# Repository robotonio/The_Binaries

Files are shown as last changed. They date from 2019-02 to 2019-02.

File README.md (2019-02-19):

# The_Binaries
This is the research project of "The Binaries" team, in the FLL "INTO ORBIT" competition, in 2019. The project's object is the exploitation of "Soft Robotics" technology in space and for this purpose, the team has developed a system which compares the pros and cons of soft &amp; hard grippers.

The name of the S/H system comes from the words Soft vs. Hard (actuators).
The main purpose of the system is to show some of the advantages of Soft Robotics in the field of actuators. The above objective should not be construed as an attempt to prove that soft actuators are "better" than traditional actuators (hard), as Soft Robotics can not substitute current technology but can help address specific problems. The system is controlled by a central console, as well as remote control (Bluetooth) via an Android application developed for that purpose.

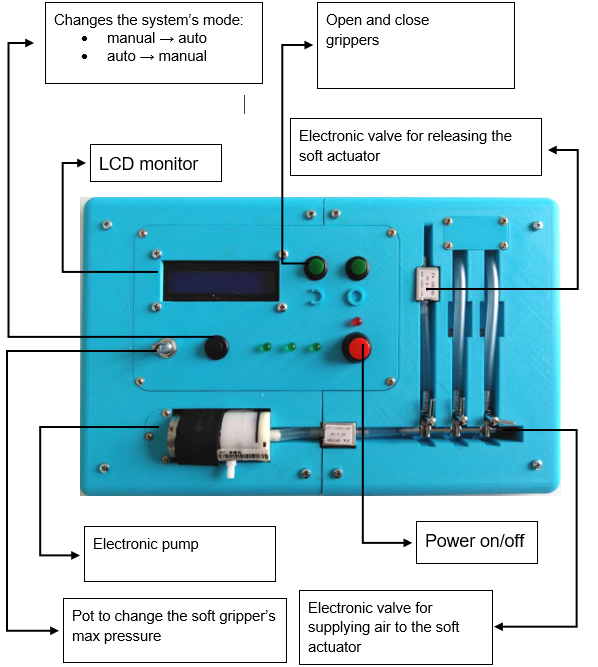
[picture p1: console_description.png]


The system is activated with the red button (B.1). When in operation, the red LED (L.1) is on, otherwise off. When the system is turned on, the THE BINARIES message appears on the LCD for 3 seconds, then the default function, which is "MANUAL," appears on the first line of the screen. The operation of the system can be changed to "AUTO" by pressing the black button (B.2) and returns to "MANUAL" in the same way.

• "MANUAL" mode: the actuators (soft & hard) open and close by pressing the green buttons B.3 & B.4 respectively. When the system is in "MANUAL" mode, the first green LED (L.2) is lit.

• "AUTO" mode: each actuator automatically closes when the ultrasonic sensor detects an object. The actuator remains closed until button B.3 is pressed. When the system is in "AUTO" mode, the second green LED (L.3) is lit.

There are also three manual air switches in the console. The first switch (S.1) should always be open to allow the Soft Actuator to bleed out. The second and third allow the air supply to the Soft Actuator to which they are connected. If the 1st actuator is used, the first switch (S.2) must be open and the 2nd switch (S.3) closed. The S.2 & S.3 switches must be inverted to activate the 2nd soft actuator.

There is also the third green LED (L.4) on the console that lights when a Bluetooth device is connected to the system. Finally, under the LCD, there is a potentiometer (P.1) used to adjust the air pressure that closes the soft actuator. The procedure for setting the pressure is as follows: the user presses B.3 for 5 seconds until "CHANGE PRESSURE" appears in the display. Then the potentiometer adjusts the desired pressure and by pressing the same button (B.3) saves the new selection.

During the operation of the system, the following useful messages are displayed on the LCD:
• During the process of setting the maximum actuator pressure, the current ("Current: #") and the new pressure ("New: #") are displayed on the LCD, where # numbers between 0 and 100.
• "HARD CLOSE" is displayed during the Hard Actuator closing process.
• The "HARD OPEN" message appears during the Hard Actuator opening process.
• In the closing procedure of the Soft Actuator, "SOFT CLOSE" appears on the first line of the LCD and the current Soft Actuator is pressed in the second.
• "SOFT OPEN" appears during the Soft Actuator opening process.

# Android APP

The Android application "THE BINARIES" has been developed for the needs of the system, which displays various measurements performed by the system and remote control of the opening and / or closing of the actuators.
The main features of the application are described below:

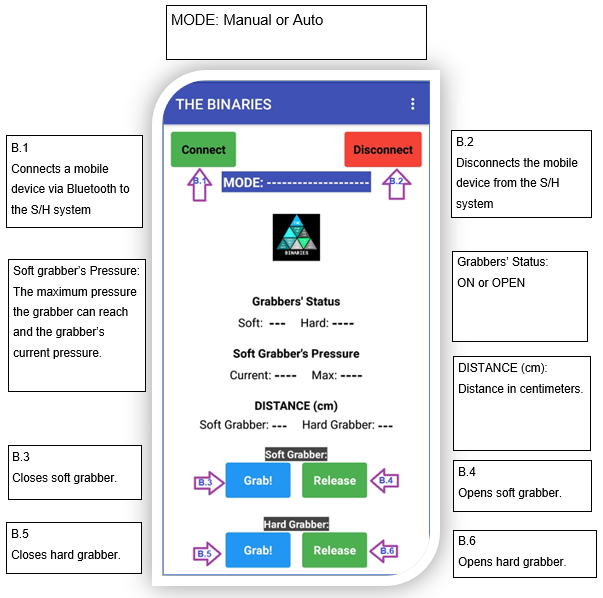
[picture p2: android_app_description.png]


# Microcontroller

The system controlled by the ESP32 microprocessor, witch has built in Bluetooth and WiFi capabilities, that make this electronic board not only autonomous to support automation but also compared to other platforms (such as those in the Arduino range), much more efficient and complete.

# Circuit

The following figure shows the system connection:

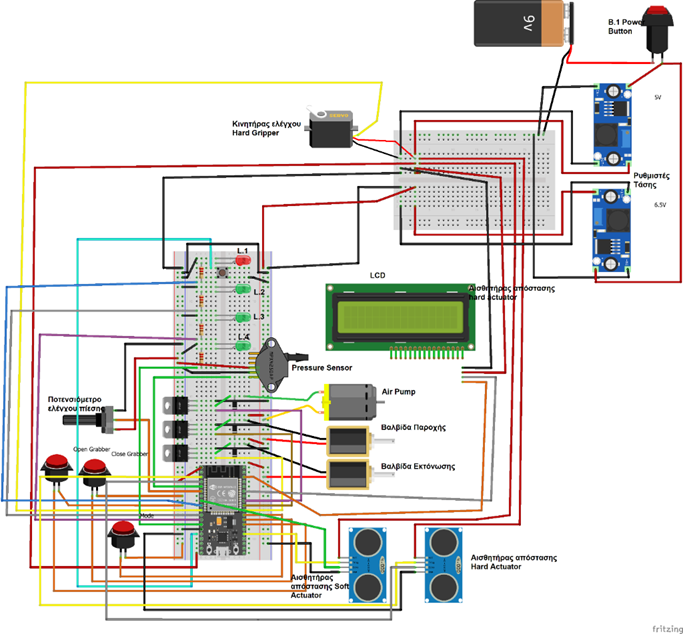
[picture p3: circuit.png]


# Sources

For the design and development of the system were used opensource sources that helped at each stage. Some of them:
1. The inspiration for the project was largely the Soft Robotics Toolkit, developed in a research conducted at Harvard University and Dublin Trinity College, which focused on the development of training kits for practical design lessons. The basic actuator control unit was based on the project "Low cost Electro-pneumatic circuit for Soft Robots", where we implemented the air supply and exhaust system in the Soft Actuator.
2. The soft actuators were built according to the instructions of the project "Air-Powered Soft Robotic Gripper" from the Instructables website.
3. For the development of the Android application-to-application code for the application (system and application side), it helped the project "ESP32 BLE + Android + Arduino IDE = AWESOME" from the Instructables website.
4. In developing the core part of the ESP32 program, he helped a lot with Adel Kassah's TUNIOT FOR ESP32 visual programming tool, based on Google's Blockly

• Soft Robotics Toolkit: https://softroboticstoolkit.com/home

• "Low cost Electro-pneumatic circuit for Soft Robots": https://softroboticstoolkit.com/low-cost-ep-circuit

• "Air-Powered Soft Robotic Gripper": https://www.instructables.com/id/Air-Powered-Soft-Robotic-Gripper/

• "ESP32 BLE + Android + Arduino IDE = AWESOME": https://www.instructables.com/id/ESP32-BLE-Android-App-Arduino-IDE-AWESOME/

• TUNIOT FOR ESP32: http://easycoding.tn/esp32/demos/code/

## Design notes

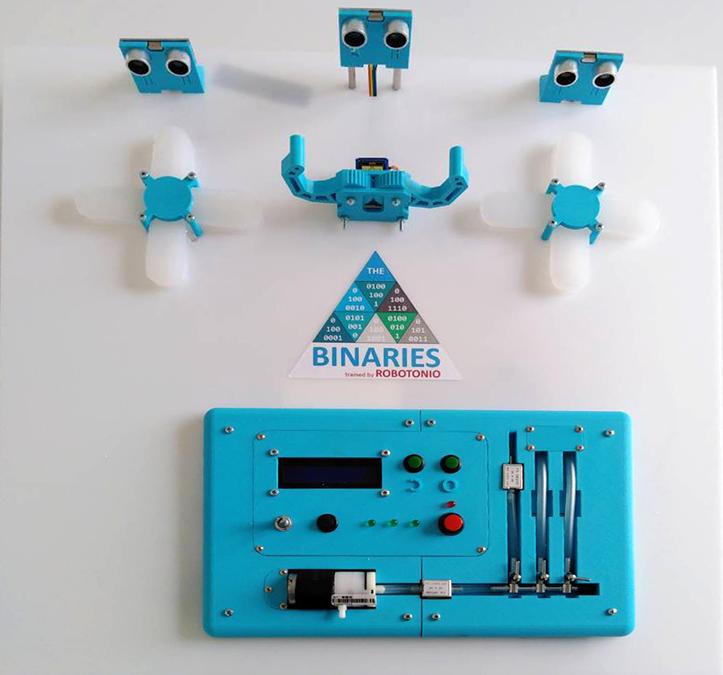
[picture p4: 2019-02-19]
console_image.jpg

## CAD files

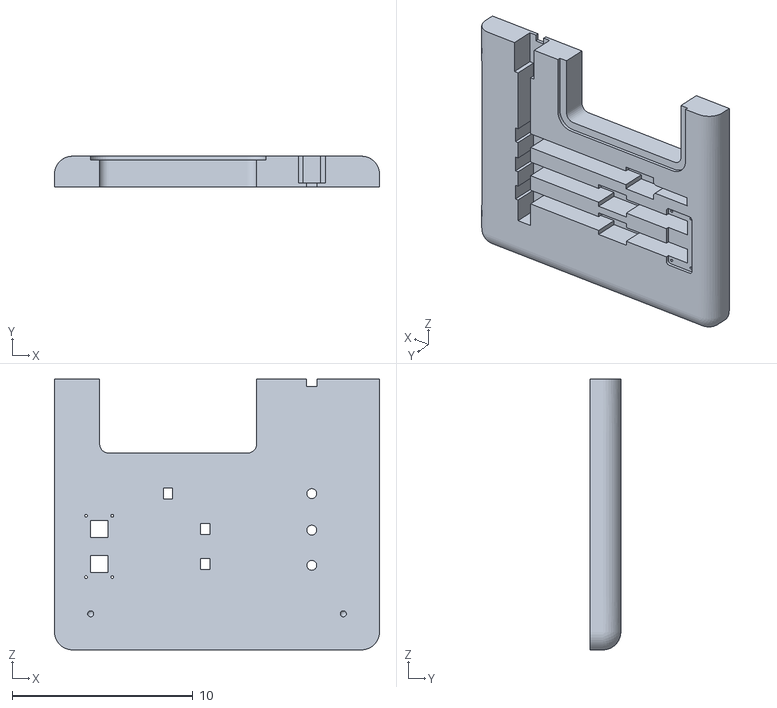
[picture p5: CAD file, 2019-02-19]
stl_files/Assembly1.stl
18.0 x 1.70 x 15.0

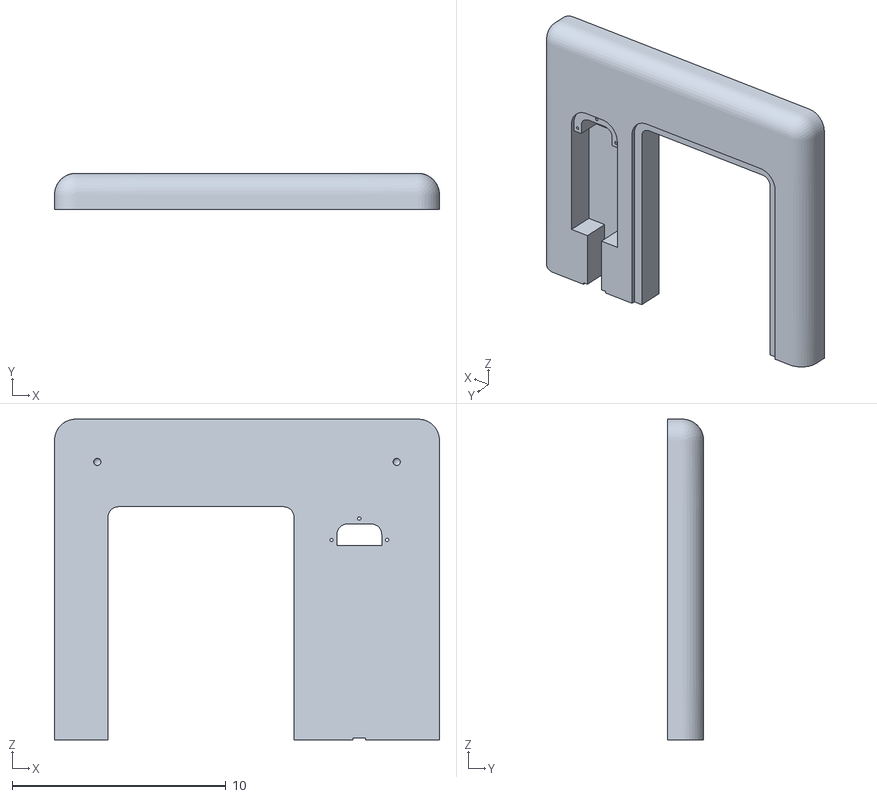
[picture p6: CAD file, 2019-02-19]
stl_files/Assembly2.stl
18.0 x 1.70 x 15.0

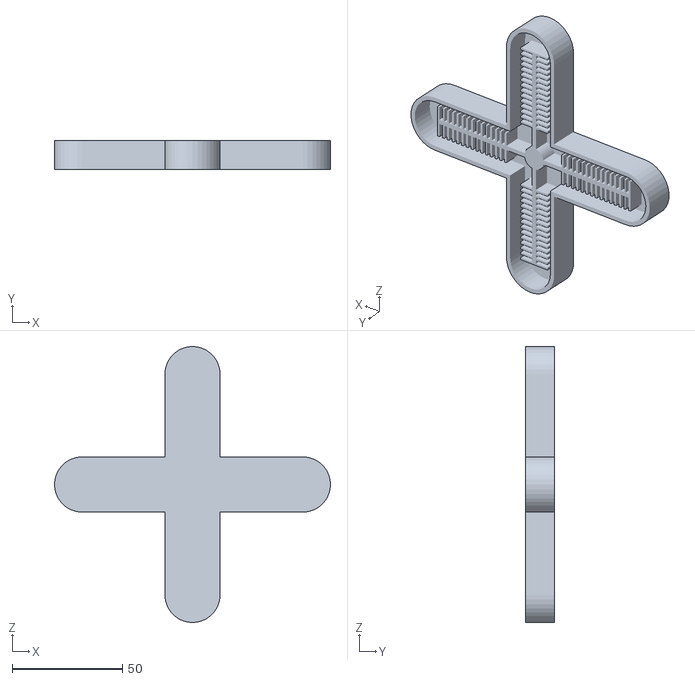
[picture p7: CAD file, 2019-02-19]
stl_files/4-leg-gripper.stl
125.0 x 13.0 x 125.0

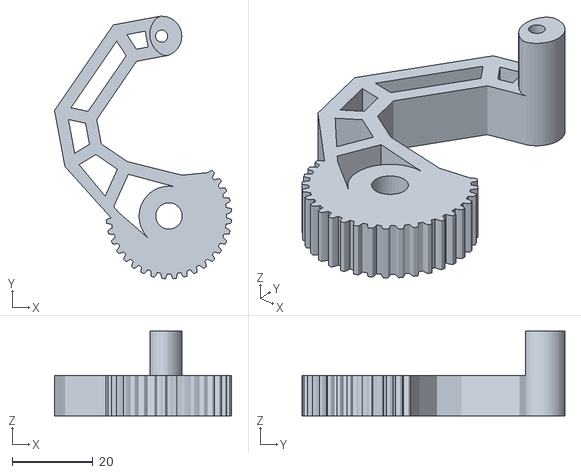
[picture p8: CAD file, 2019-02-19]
stl_files/stl_hard_gripper/finger-left-thin.stl
44.0 x 65.2 x 21.0

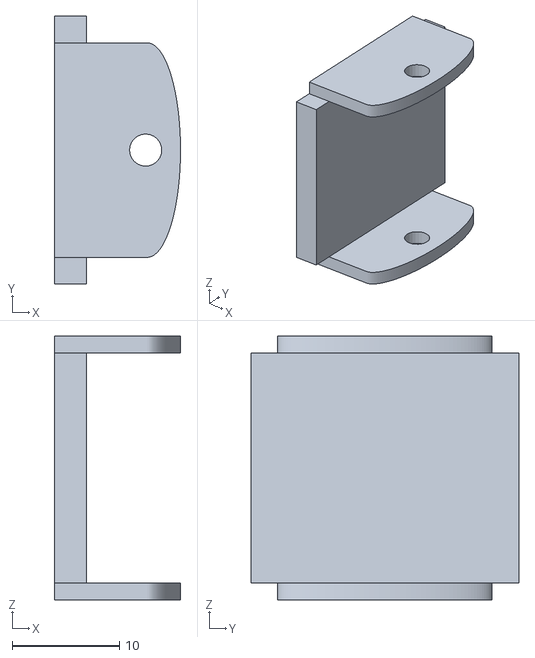
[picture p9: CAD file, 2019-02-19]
stl_files/stl_hard_gripper/finger-pad.stl
11.8 x 25.0 x 24.6

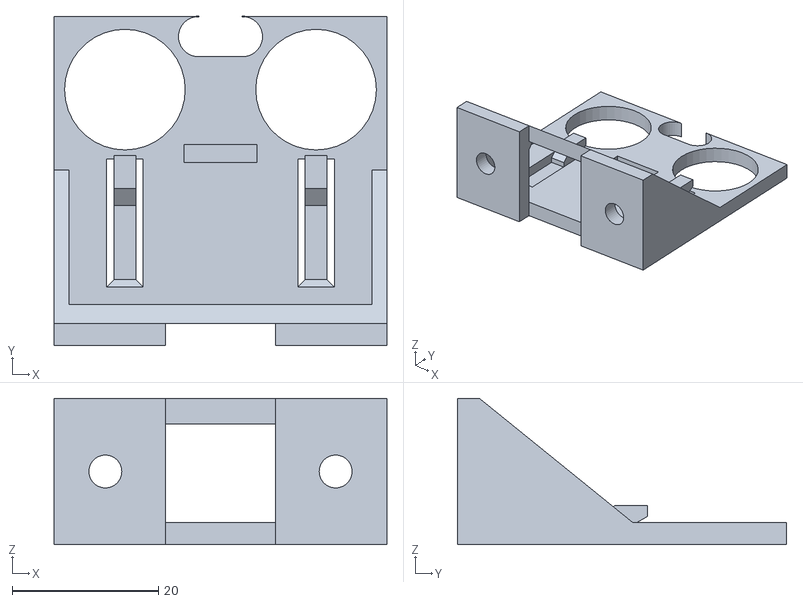
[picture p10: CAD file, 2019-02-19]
stl_files/Ultrasonic_HC-SR04_-_FOOT_MOUNT.stl
45.5 x 45.0 x 20.0

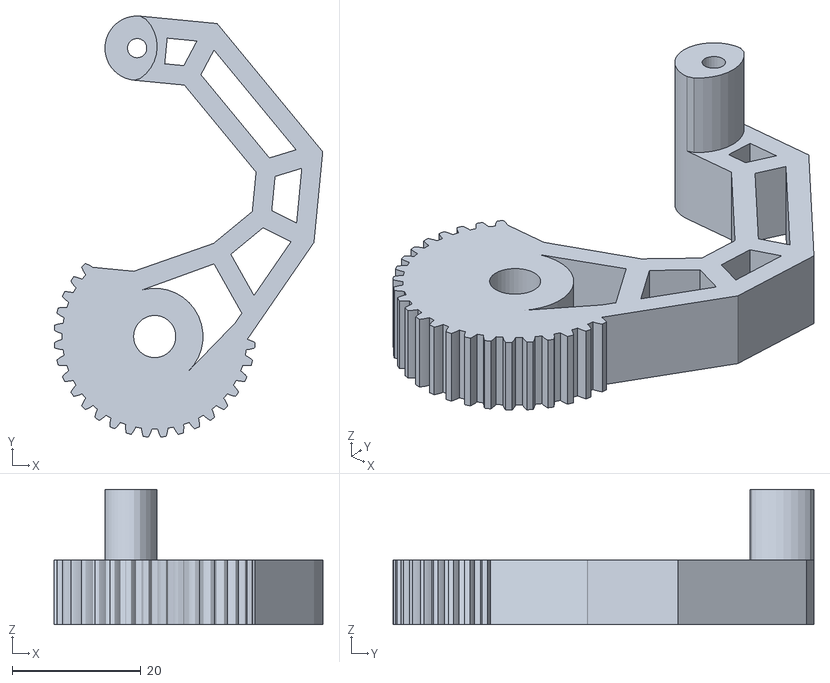
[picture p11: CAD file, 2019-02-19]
stl_files/stl_hard_gripper/finger-right-thin.stl
41.7 x 65.4 x 21.0

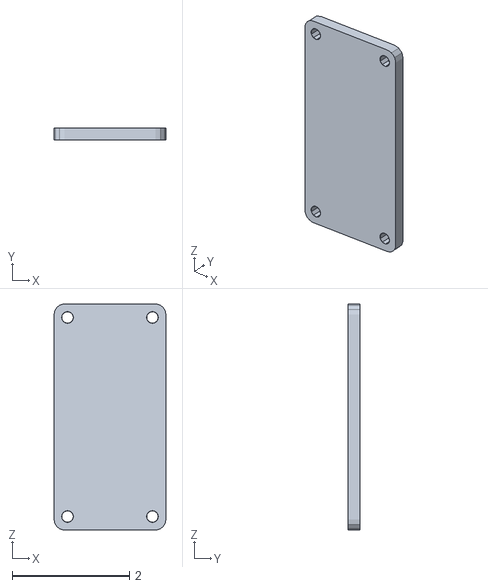
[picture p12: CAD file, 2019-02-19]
stl_files/Part2 base.stl
1.91 x 0.2 x 3.86

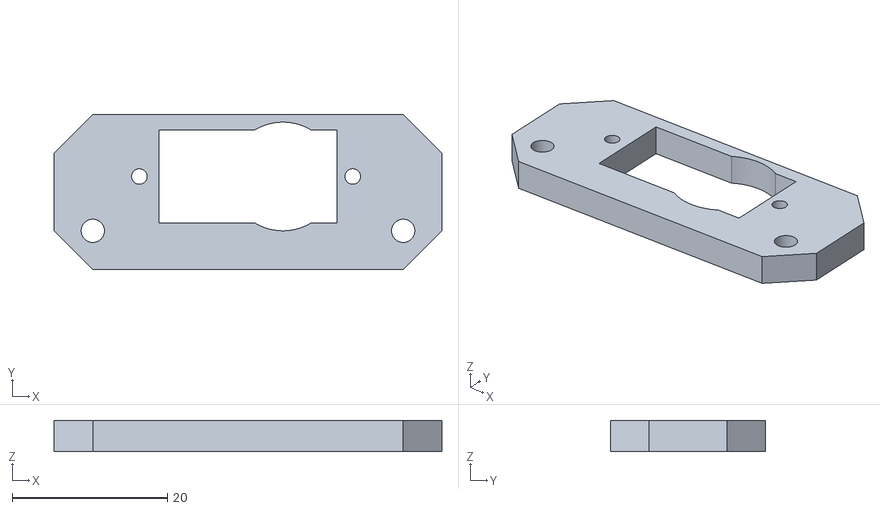
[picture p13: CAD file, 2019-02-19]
stl_files/stl_hard_gripper/servo-spacer-bigger.stl
50.0 x 20.0 x 4.00

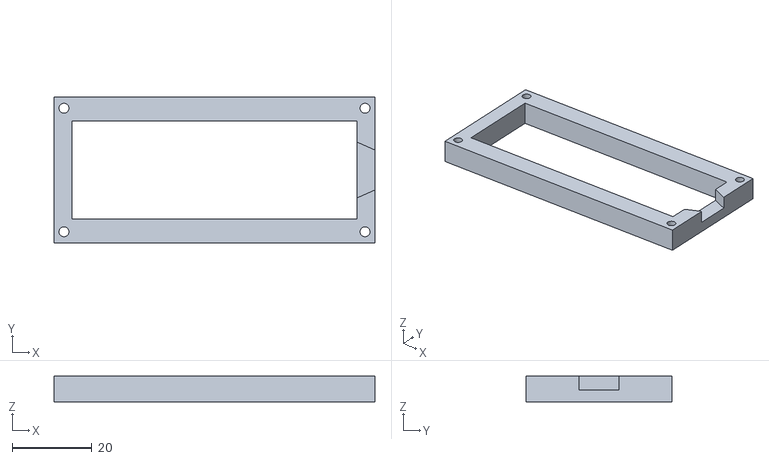
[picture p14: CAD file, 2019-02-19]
stl_files/lcd spacer.stl
80.5 x 36.5 x 6.50

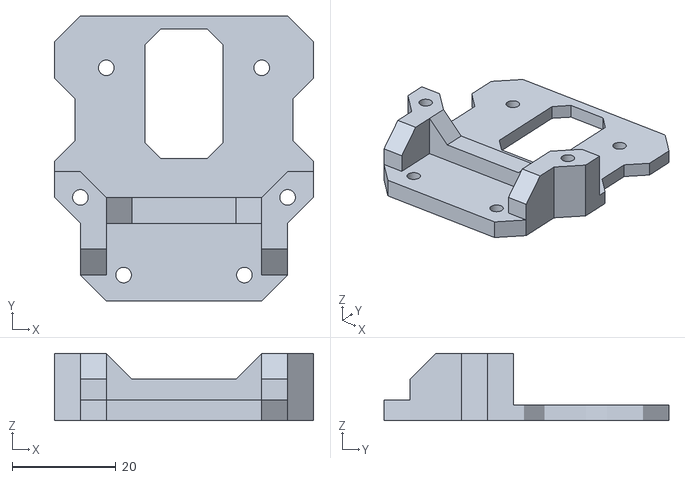
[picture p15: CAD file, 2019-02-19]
stl_files/stl_hard_gripper/gripper-base-thin.stl
50.0 x 55.0 x 13.0

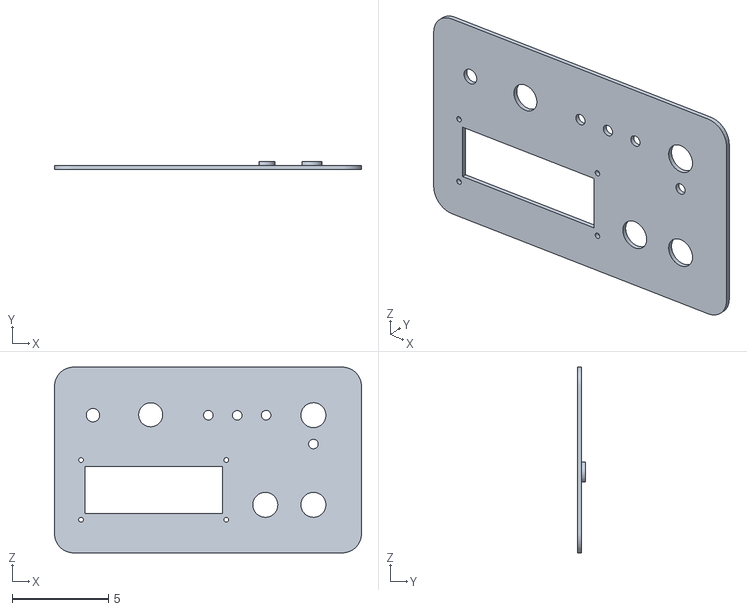
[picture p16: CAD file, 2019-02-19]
stl_files/lcd.stl
16.0 x 0.4 x 9.66

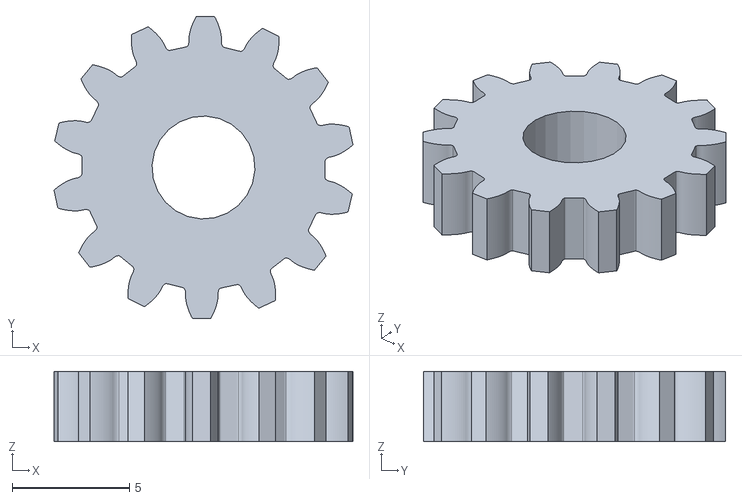
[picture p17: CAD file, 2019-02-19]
stl_files/stl_hard_gripper/servo-gear.stl
12.8 x 12.9 x 3.00

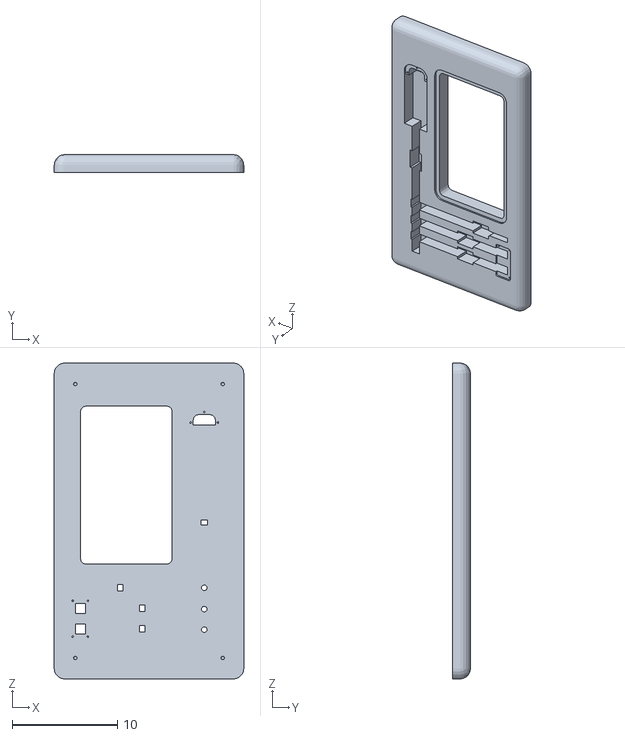
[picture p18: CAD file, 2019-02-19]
stl_files/Project FLL 2019 Base Final.stl
18.0 x 1.70 x 30.0

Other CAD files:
stl_files/stl_hard_gripper/top-plate-fixed.stl
stl_files/Part1 base.stl
stl_files/stl_hard_gripper/finger-bushing-thin.stl
stl_files/stl_hard_gripper/test.stl
stl_files/stand soft cross.stl

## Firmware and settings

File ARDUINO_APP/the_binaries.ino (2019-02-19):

#include <BLEDevice.h>
#include <BLEServer.h>
#include <BLEUtils.h>
#include <BLE2902.h>
#include <Servo.h>
#include <LiquidCrystal_I2C.h> //for LCD I2C

/* Bluetooth configuration*/
BLECharacteristic *pCharacteristic;
bool deviceConnected = false;
// See the following for generating UUIDs:
// https://www.uuidgenerator.net/
#define SERVICE_UUID           "6E400001-B5A3-F393-E0A9-E50E24DCCA9E" // UART service UUID
#define CHARACTERISTIC_UUID_RX "6E400002-B5A3-F393-E0A9-E50E24DCCA9E"
#define CHARACTERISTIC_UUID_TX "6E400003-B5A3-F393-E0A9-E50E24DCCA9E"

/*
 * usefull variables
*/
// max soft grabber's pressure in  
int maxPressure = 25; //calibrate it! (< 100)
int modeNumber = 1; //mode = 1 in setup
int previousMode = 1; //keep previous mode to know new change
//the max and min servo angle for hard actuator (calibrate it!)
int servoOpenDegrees = 180;//close
int servoCloseDegrees = 50;//open
//the distance threshold than actuate soft grabber in cm (calibrate it!)
int actDistanceSoft = 10;
//the distance threshold than actuate hard grabber in cm (calibrate it!)
int actDistanceHard = 10;
//flag for soft actuator (open/closed)
boolean softIsOpen = true;
//flag for hard actuator (open/closed)
boolean hardIsOpen = true;
long lastBTms = 0;//last communication with bluetooth 
long btSlot = 1000; //send bluetooth data every btSlot milliseconds
char BT_data[23];//buffer to keep data for bluetooth devices
long interruptTime = 0;
boolean interruptFlag = true;

void releaseSoft();
void releaseHard();
void grabSoft();
void grabHard();
bool is_number(const std::string& s);
class MyServerCallbacks: public BLEServerCallbacks {
    void onConnect(BLEServer* pServer) {
      deviceConnected = true;
    };

    void onDisconnect(BLEServer* pServer) {
      deviceConnected = false;
    }
};

class MyCallbacks: public BLECharacteristicCallbacks {
    void onWrite(BLECharacteristic *pCharacteristic) {
      std::string rxValue = pCharacteristic->getValue();

      if (rxValue.length() > 0) {
        Serial.println("*********");
        Serial.print("Received Value: ");

        for (int i = 0; i < rxValue.length(); i++) {
          Serial.print(rxValue[i]);
        }

        Serial.println();

        // Do stuff based on the command received from the app
        if (rxValue.find("S0") != -1) { 
          Serial.print("Soft Release");
          releaseSoft();
        } else if (rxValue.find("S1") != -1) { 
          Serial.print("Soft Grab");
          grabSoft();
        } else if (rxValue.find("H0") != -1) { 
          Serial.print("Hard Release");
          releaseHard();
        } else if (rxValue.find("H1") != -1) { 
          Serial.print("Hard Grab");
          grabHard();
        } else {
          Serial.print("New pressure");
          int newMaxPressure = atoi(rxValue.c_str());//std::stoi(rxValue);
          if(newMaxPressure > 0 && newMaxPressure < 100){
            maxPressure = newMaxPressure;
          }
        }

        Serial.println();
        Serial.println("*********");
      }
    }
};


LiquidCrystal_I2C lcd(0x3f, 16, 2);
Servo servo;

/*
 * Modes:
 *  1: on / off buttons (same for soft & hard gribbers)
 *  2: ultrasonic sensor use
 *  3: bluetooth use
*/

/*
 * All the pins
*/
// power button
int pinLedPower = 25;
// on-off buttons mode LED
int pinLedMode1 = 12;
// ultrasonic mode LED
int pinLedMode2 = 14;
// bluetooth mode LED
int pinLedMode3 = 4;
// change mode button
int pinModeBtn = 17;
// pressure configuration pot
int pinPressurePot = 35;
// change max pressure button
int pinPressureButton = 13;
// open grippers button
int pinOpenButton = 27;
// close grippers button
int pinCloseButton = 16;
// pressure sensor
int pinPressureSensor = 34;
// servo motor
int pinServo = 26;
// solenoid inflate gripper
int pinSolenoidInflate = 5;
// solenoid expansion gripper
int pinSolenoidExpanse = 18;
// dc motor (to close soft gripper)
int pinMotor = 19;
// Ultrasonic for soft gripper
int pinTrigHcSoft = 36;//2;
int pinEchoHcSoft = 39;//33;
// Ultrasonic for hard gripper
int pinTrigHcHard = 2;//36;
int pinEchoHcHard = 33;//39;
// Ultrasonic for 2nd soft gripper
int pinTrigHcSoft2 = 32;
int pinEchoHcSoft2 = 15;



/*
 * This function is triggered when a new
 * interrupt happens. In this way we change
 * the mode, using the mode button
*/
void handleModeInterrupt(){
  //move modeNumber to next mode
  interruptTime = millis();
  if(interruptFlag){
    modeNumber++;
    //max modeNumber is 2
    if(modeNumber > 2){
      modeNumber = 1;
    }
  }
}

void setup() {
  Serial.begin(115200);
  //configure servo for hard actuator
  servo.attach(pinServo);
  servo.write(servoOpenDegrees);//in setup hard actuator is closed
  //configure LCD
  lcd.init();
  lcd.backlight();
  //configure soft Ultrasonic Sensor
  pinMode(pinTrigHcSoft, OUTPUT); // Sets the trigPin as an Output
  pinMode(pinEchoHcSoft, INPUT); // Sets the echoPin as an Input
  //configure soft Ultrasonic Sensor
  pinMode(pinTrigHcSoft2, OUTPUT); // Sets the trigPin as an Output
  pinMode(pinEchoHcSoft2, INPUT); // Sets the echoPin as an Input
  //configure hard Ultrasonic Sensor
  pinMode(pinTrigHcHard, OUTPUT); // Sets the trigPin as an Output
  pinMode(pinEchoHcHard, INPUT); // Sets the echoPin as an Input
  //configure LEDs
  pinMode(pinLedPower, OUTPUT);
  pinMode(pinLedMode1, OUTPUT);
  pinMode(pinLedMode2, OUTPUT);
  pinMode(pinLedMode3, OUTPUT);
  //configure buttons
  pinMode(pinModeBtn, INPUT_PULLUP);
  pinMode(pinOpenButton, INPUT_PULLUP);
  pinMode(pinCloseButton, INPUT_PULLUP);
  pinMode(pinPressureButton, INPUT_PULLUP);
  //configure motors
  pinMode(pinSolenoidInflate, OUTPUT);
  pinMode(pinSolenoidExpanse, OUTPUT);
  pinMode(pinMotor, OUTPUT);

  //initialise actuators (all closed)
  digitalWrite(pinSolenoidInflate, LOW);
  digitalWrite(pinSolenoidExpanse, LOW);
  digitalWrite(pinMotor, LOW);

  //initialise LEDs (in setup mode=1)
  digitalWrite(pinLedPower, HIGH);//never changes
  digitalWrite(pinLedMode1, HIGH);
  digitalWrite(pinLedMode2, LOW);
  digitalWrite(pinLedMode3, LOW);
  setMode(modeNumber);
  //configure interrupt to change mode
  attachInterrupt(digitalPinToInterrupt(pinModeBtn), handleModeInterrupt, FALLING);

  /* Bluetooth set up*/
  // Create the BLE Device
  BLEDevice::init("THE_BINARIES"); // Give it a name

  // Create the BLE Server
  BLEServer *pServer = BLEDevice::createServer();
  pServer->setCallbacks(new MyServerCallbacks());

  // Create the BLE Service
  BLEService *pService = pServer->createService(SERVICE_UUID);

  // Create a BLE Characteristic
  pCharacteristic = pService->createCharacteristic(
                      CHARACTERISTIC_UUID_TX,
                      BLECharacteristic::PROPERTY_NOTIFY
                    );
                      
  pCharacteristic->addDescriptor(new BLE2902());

  BLECharacteristic *pCharacteristic = pService->createCharacteristic(
                                         CHARACTERISTIC_UUID_RX,
                                         BLECharacteristic::PROPERTY_WRITE
                                       );

  pCharacteristic->setCallbacks(new MyCallbacks());

  // Start the service
  pService->start();

  // Start advertising
  pServer->getAdvertising()->start();

  /* End bluetooth configuration*/
}

void loop() {
  //check id modeNumber changed to update the system mode
  if(millis() - interruptTime > 1000){
    interruptFlag = true;
  }
  if(previousMode != modeNumber){
    digitalWrite(pinSolenoidExpanse, HIGH);
    interruptFlag = false;
    setMode(modeNumber);
    previousMode = modeNumber;//update previousMode
  }
  //mode options
  if(modeNumber == 1){//move actuators with buttons
    runMode1();
  } else if(modeNumber == 2){//grab with sensor and free with button
    runMode2();
  }
  //check pressure button to change max pressure
  if(digitalRead(pinPressureButton) == LOW){
    Serial.println("pinPressureButton pressed");
    controlMaxPressure();    
  }

  if(millis() - lastBTms > btSlot){
    bluetoothApp();
    lastBTms = millis();
  }
}

/*
 * Control both actuators with the 
 * grab&free buttons
*/
void runMode1(){
  if(digitalRead(pinOpenButton) == LOW){
    long openTime = millis();
    boolean pressureMode = false;
    while(digitalRead(pinOpenButton) == LOW){
      if(millis() - openTime > 3000){
        pressureMode = true;
        break;
      } 
    }
    if(pressureMode){
      controlMaxPressure();
    } else {
      Serial.println("open button");
      releaseSoft();
      releaseHard();
      delay(500); 
    }
  }
  if(digitalRead(pinCloseButton) == LOW){
    Serial.println("close button");
    grabSoft();
    grabHard();
    delay(500);
  }
}


/*
 * Control actuators with ultrasonic sensors
 * The actuator will grab when it's distance 
 * sensor detect an object and will free thw object
 * when user push the release button 
*/
void runMode2(){
  //grab when detect object AND actuator is open
  int softDistance = readDistance(1);
  int hardDistance = readDistance(2);
  int softDistance2 = readDistance(3);
  Serial.print("Soft distance 1: ");
  Serial.println(softDistance);
  Serial.print("Hard distance: ");
  Serial.println(hardDistance);
  Serial.print("Soft distance 2: ");
  Serial.println(softDistance2);
  if((softDistance < actDistanceSoft || softDistance2 < actDistanceSoft) && softIsOpen){
    grabSoft();
  }
  //grab when detect object AND actuator is open
  if(hardDistance < actDistanceHard && hardIsOpen){
    grabHard();
  }
  //release object after push the release button
  if(digitalRead(pinOpenButton) == LOW){
    //protect actuator if is already open
    if(!softIsOpen){
      releaseSoft();  
    }
    //protect actuator if is already open
    if(!hardIsOpen){
      releaseHard();  
    }
  }
}

void bluetoothApp(){
  if (deviceConnected) {
    digitalWrite(pinLedMode3, HIGH);
    updateData();
    Serial.print("*** Sent Value: ");
    Serial.print(BT_data);
    Serial.println(" ***");
    
    pCharacteristic->setValue(BT_data);
    pCharacteristic->notify(); // Send the value to the app!
  } else {
    digitalWrite(pinLedMode3, LOW);
  }
}

/*
 * Control the max pressure of the closed soft
 * grabber, with the pot
*/
void controlMaxPressure(){
  // warn user with LCD message for 3 seconds
  for(int i = 0; i < 3; i++){
    lcd.clear();
    lcd.setCursor(0,0);
    lcd.print("CHANGE PRESSURE");
    delay(1000);
  }
  //old max pressure at the first line of LCD
  lcd.clear();
  lcd.setCursor(0,0);
  lcd.print("Current: ");
  lcd.setCursor(10,0);
  lcd.print(maxPressure);
  lcd.setCursor(0,1);
  //pot value at the first line of LCD, until push pinPressureButton
  lcd.print("New: ");
  while(digitalRead(pinOpenButton) == HIGH){
    lcd.setCursor(6,1);
    lcd.print("    ");
    lcd.setCursor(6,1);
    lcd.print((analogRead(pinPressurePot)*100)/4095);
    delay(300);
  }
  //change max pressure
  maxPressure = (analogRead(pinPressurePot)*100)/4095;
  // restore mode
  setMode(modeNumber);
  delay(1000);
}

/*
 * For soft grabber, gr == 1 
 * For hard grabber, gr == 2
 */
int readDistance(byte gr){
  int tr = 0;
  int ech = 0;
  long duration;
  //use the right ultrasonic pins
  if(gr == 1){
    tr = pinTrigHcSoft;
    ech = pinEchoHcSoft;
  }
  if(gr == 2){
    tr = pinTrigHcHard;
    ech = pinEchoHcHard;
  }
  if(gr == 3){
    tr = pinTrigHcSoft2;
    ech = pinEchoHcSoft2;
  }
  // Clears the trigPin
  digitalWrite(tr, LOW);
  delayMicroseconds(2);
  
  // Sets the trigPin on HIGH state for 10 micro seconds
  digitalWrite(tr, HIGH);
  delayMicroseconds(10);
  digitalWrite(tr, LOW);
  
  // Reads the echoPin, returns the sound wave travel time in microseconds
  duration = pulseIn(ech, HIGH);
  
  // return the distance in CMs
  return duration*0.034/2;
}

/*
 * Simple returns the soft actuator's pressure
 * in the range of 0-4095
*/
int readPressure(){
  return (analogRead(pinPressureSensor)*100)/4095;//
}

/*
 * Grab an object with the soft actuator
*/
void grabSoft(){
  Serial.println("grab soft - start");
  //protect the grabber if is already closed
  if(!softIsOpen){
    return;
  }
  //update LCD info
  lcd.setCursor(0, 1);
  lcd.print("               ");
  lcd.setCursor(0, 1);
  lcd.print("CLOSE:");
  //open inflate solinoid
  digitalWrite(pinSolenoidInflate, HIGH);
  //open expanse solinoid
  digitalWrite(pinSolenoidExpanse, LOW);
  //actuate motor to inflate soft grabber
  digitalWrite(pinMotor, HIGH);
  //inflate until air pressure is fine or until press open button (for safe)
  while(readPressure() < maxPressure && digitalRead(pinOpenButton) == HIGH){
    lcd.setCursor(8, 1);
    lcd.print("     ");
    lcd.setCursor(8, 1);
    lcd.print(readPressure());
    delay(50);
  }
  digitalWrite(pinSolenoidInflate, LOW);
  digitalWrite(pinMotor, LOW);
  lcd.setCursor(8, 1);
  lcd.print("     ");
  lcd.setCursor(8, 1);
  lcd.print(readPressure());
  //stop inflation
  
  //change soft grabber status to closed
  softIsOpen = false;
  Serial.println("grab soft - end");
}

void releaseSoft(){
  Serial.println("release soft - start");
  //protect the grabber if is already closed
  if(softIsOpen){
    return;
  }
  //update LCD info
  lcd.setCursor(0, 1);
  lcd.print("               ");
  lcd.setCursor(0, 1);
  lcd.print("SOFT OPEN");
  digitalWrite(pinSolenoidExpanse, HIGH);
  delay(2000);
  digitalWrite(pinSolenoidExpanse, LOW);
  lcd.setCursor(0, 1);
  lcd.print("               ");
  softIsOpen = true;
  Serial.println("release soft - end");
}

void grabHard(){
  Serial.println("grab hard");
  //protect the grabber if is already closed
  if(!hardIsOpen){
    return;
  }
  //update LCD info
  lcd.setCursor(0, 1);
  lcd.print("               ");
  lcd.setCursor(0, 1);
  lcd.print("HARD CLOSE");
  //close hard grabber slowly
  for(int i = servoOpenDegrees; i > servoCloseDegrees; i--){
    servo.write(i);
    delay(10);//change it if it's too slow or fast!
  }
  //change hard grabber status to closed
  hardIsOpen = false;
  Serial.println("grab hard - end");
}

void releaseHard(){
  Serial.println("release hard");
  if(hardIsOpen){
    return;
  }
  //update LCD info
  lcd.setCursor(0, 1);
  lcd.print("               ");
  lcd.setCursor(0, 1);
  lcd.print("HARD OPEN");
  for(int i = servoCloseDegrees; i < servoOpenDegrees; i++){
    servo.write(i);
    delay(10);
  }
  lcd.setCursor(0, 1);
  lcd.print("               ");
  hardIsOpen = true;
  Serial.println("release hard - end");
}

void setMode(int m){
  Serial.print("New Mode:");
  Serial.println(m);
  String msg = "";
  modeNumber = m;
  lcd.clear();
  lcd.setCursor(0, 0);
  if(modeNumber == 1){
    digitalWrite(pinLedMode1, HIGH);
    digitalWrite(pinLedMode2, LOW);
    digitalWrite(pinLedMode3, LOW);
    lcd.print("Mode: MANUAL");
  } else if(modeNumber == 2){
    digitalWrite(pinLedMode1, LOW);
    digitalWrite(pinLedMode2, HIGH);
    digitalWrite(pinLedMode3, LOW);
    lcd.print("Mode: AUTO");
  } 
  delay(1000);
}

/* update the char array BT_data to send it to bluetooth device*/
void updateData(){
    
    String str;
    //1. mode number
    str = String(modeNumber);
    int index = 0;
    for(int i = 0; i < str.length(); i++){
      BT_data[index++] = str[i];
    }
    BT_data[index++] = ' ';
    //2. soft actuator status
    if(softIsOpen){
      BT_data[index++] = '0';
    } else {
      BT_data[index++] = '1';
    }
    BT_data[index++] = ' ';
    //3. hard actuator status
    if(hardIsOpen){
      BT_data[index++] = '0';
    } else {
      BT_data[index++] = '1';
    }
    BT_data[index++] = ' ';
    //4. max pressure
    str = String(maxPressure);
    for(int i = 0; i < str.length(); i++){
      BT_data[index++] = str[i];
    }
    BT_data[index++] = ' ';
    //5. current pressure
    str = String(readPressure());
    for(int i = 0; i < str.length(); i++){
      BT_data[index++] = str[i];
    }
    BT_data[index++] = ' ';
    //6. soft actuator distance (get min)
    int minDistance = readDistance(1);
    if(readDistance(3) < minDistance){
      minDistance = readDistance(3);
    }
    str = String(minDistance);
    for(int i = 0; i < str.length(); i++){
      BT_data[index++] = str[i];
    }
    BT_data[index++] = ' ';
    //7. hard actuator distance
    str = String(readDistance(2));
    for(int i = 0; i < str.length(); i++){
      BT_data[index++] = str[i];
    }
    BT_data[index] = '\0';
}

bool is_number(const std::string& s)
{
    std::string::const_iterator it = s.begin();
    while (it != s.end() && std::isdigit(*it)) ++it;
    return !s.empty() && it == s.end();
}

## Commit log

2019-02-19 Console Brief Description
    Α brief description of the console's operation
2019-02-19 Circuit
    The system circuit
2019-02-19 Hard gripper stl files
    These files comes from https://www.thingiverse.com/thing:3056229
    [finger-bushing-thin.stl, finger-left-thin.stl, finger-pad.stl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]
2019-02-19 The mold of the soft actuator
    Source: https://www.instructables.com/id/Air-Powered-Soft-Robotic-Gripper/
    [4-leg-gripper.stl]
